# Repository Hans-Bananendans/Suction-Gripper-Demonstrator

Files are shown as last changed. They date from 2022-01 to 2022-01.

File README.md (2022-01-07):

# Suction-Gripper-Demonstrator
Repository that contains a blueprint for a demonstrator model of a bio-inspired, suction-based gripper. This demonstrator was developed by a student team as part of a Bio-Inspired Design MSc course.

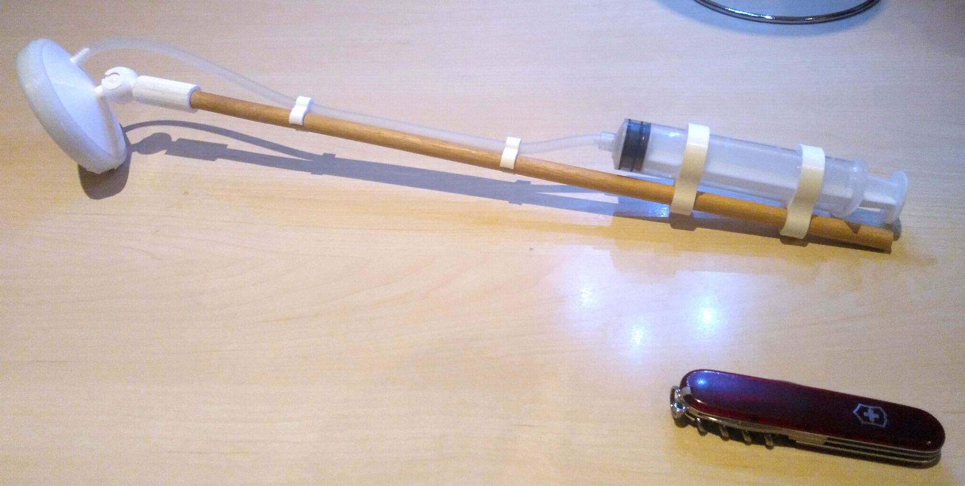
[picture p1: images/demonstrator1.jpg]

_Picture of the demonstrator (Swiss army knife for scale)_

## Description
What this gripper demonstrator is supposed to "demonstrate" is that an array of compliant suction cups can be used to generate substantial gripping force. A miniaturized derivative of such a design could potentially be used in medical applications as a surgical gripper, the current designs of which frequently feature metal "jaws" that often inflict unwanted trauma during surgery due to excess force. A suction-based gripper could spread this force out over a larger area and reduce the chance of complications.

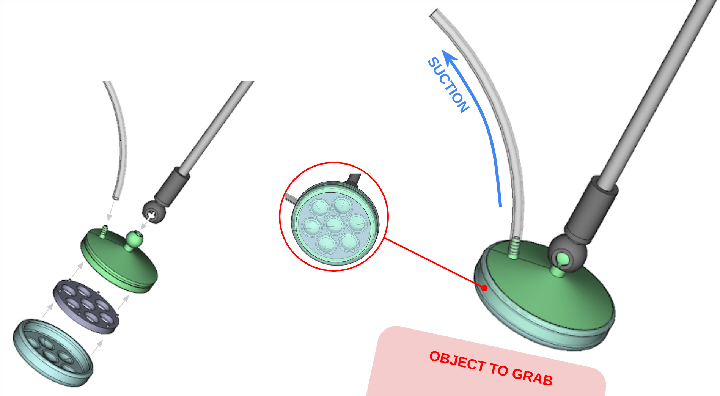
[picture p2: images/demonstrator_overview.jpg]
demonstrator_overview


The demonstrator works as follows: It features a head which can be used to "grip" objects. This head consists of a compliant (~Shore 30) material whose shape can be changed. Inside the head is a sealed chamber, and when pressure in the chamber is reduced, it pulls the compliant material inside. The compliant material is deformed in such a way that it creates suction cups on the other side, which then create a suction force between the head and whatever object is being grabbed. Many cephalopods use a similar principle to attach their limbs to many different objects, and as such, this design was inspired by these animals.

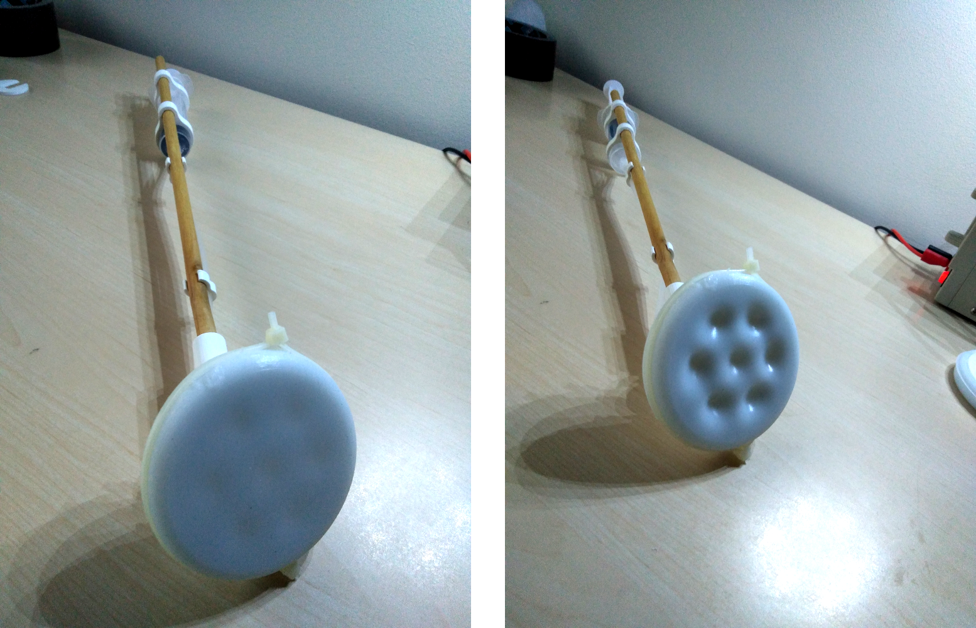
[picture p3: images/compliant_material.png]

_Compliant head of the suction gripper in action. On the right, the syringe is used to reduce the pressure in the suction head to create small suction cups._

## Printable components
For the demonstrator model, some parts will have to be printed. This can be done out of PLA, and the printer does not have to be terribly fancy. The author used an Ender 3 Pro printer for all prints. The STL-files for the prints can be found in the `./STL/` folder.

To build the depicted demonstrator model, you will need to print the following parts:
| Qty | Part | Comment |
| --- |:---|:---|
| 1 | `silicone_mould_bottom_v2.stl` | Print such that the side with the casting negative is pointing up. |
| 1 | `silicone_mould_top_v2.stl` | Print such that the side with the casting negative is pointing up. |
| 1 | `silicone_mould_funnel.stl` | Print with the small side pointing up. |
| 1 | `stick_socket.stl` | Print such that the joint socket is pointing up. |
| 1 | `suction_head_casing.stl` | Print with the ball joint pointing up. |
| 1 | `suction_head_gridcover.stl` | Print with the small knobs pointing up. |
| 2 | `syringe_coupler.stl` | - |
| 2 | `tube_coupler.stl` | - |
| 1 | `syringe_lock.stl` | Optional if you want to lock the syringe in place. |

Printing settings used by author:
 - 20% filler or more.
 - <20 mm/s speed
 - <0.2 mm layer height
 - 1.2 mm wall thickness
 - Use tree supports for everything.

## Component list
**Materials/consumables**
 - 1 30 mL medical syringe
 - ~0.5 meters of medical tubing (4.5 mm inner diameter)
 - A mounting stick. The author used a 400 mm long wooden stick of 9.5 mm diameter.
 - PLA parts as listed above.
 - Super glue (such as cyanoacrylate).
 - Silicone-based kit or glue (the author used [Bison Poly Max](https://www.bison.net/en/product.6310168)). Many other glues (epoxy, cyanoacrylate, etc.) will **NOT** bond with silicone!
 - Latex/vinyl gloves.
 - Some zip ties.
 - Pourable silicone mix (the author used [Wilsor two-component silicone](https://www.wilsor.nl/product/siliconen-rubber/)).
 - Mixing cup for the silicone casting.
 - A stirring implement such as a wooden stick, for the silicone casting.
 - Kitchen scales.
 - Paper towels.

**Tools**
 - Duct tape.
 - Gluing clamps.
 - 120 grit and 400 grit sandpaper.
 - Vaseline.
 - Small files.
 - Hobby knife/army knife.
 - Calipers.

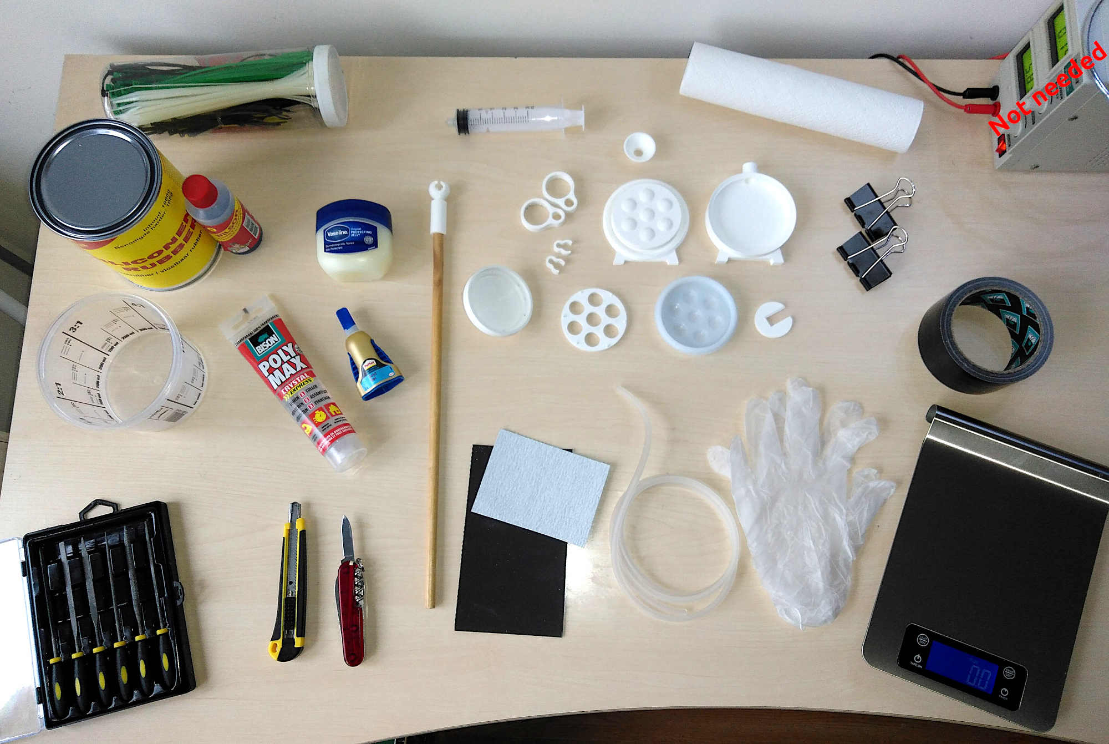
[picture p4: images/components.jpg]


## Manufacturing and assembly

1. First print the parts, as this will take the most time. Gather all the other required tools in the meantime.

### Post-processing the 3D printed parts
2. Remove the excess supports on the printed parts.
3. Test the fit of the `suction_head_casing` and the `suction_head_gridcover`. Remove excess material from the outer edge and the six knobs of the `suction_head_gridcover`, and ensure that the six holes in the `suction_head_casing` are large enough. In the end, you should have a snug fit.
4. Carefully remove the excess material from the outer tube gasket, so that it will not leak when a tube is attached to it.
5. Sand the ball joint until smooth.
6. Using the 120 grit sandpaper, smooth the inner surfaces of the mould halves. Then continue this using 400 grit wet sanding, until the inner surfaces are nice and smooth. Any irregularities in these surfaces will show up in the silicone component as well so to prevent leaks, ensure that the inside of the mould is nice and smooth.
7. Using a small amount of super glue, bond the mould funnel to the mould bottom part. This will form the channel into which the silicone mixture will be poured. The mould is designed such that this channel is also the only riser, allowing for bubbles to escape from the same hole. The funnel will also ensure an excess of silicone at the top, allowing the fluid pressure to force the silicone into the mould.

### Casting the silicone component
8. Coat the inside of the mould with a thin layer of vaseline, so that the silicone cast will release easily. 
9. Close the mould halves and fix them in places using duct tape and/or gluing clamps. The mould is designed with inclined edges such that the two parts will centre by themselves. Ensure that the little feet on both sides of the mould align with one another properly, otherwise the mould will wobble during the casting process. 
10. Put on your gloves. Weigh off around 40-50 grams of silicone base, and mix it with the hardening component in the mixing ratio specified by the manufacturer. For the Winsor silicone used by the author, the base:hardener mixing ratio is 40:3. Stir for a few minutes until the components are thoroughly mixed.
11. Carefully pour the silicone mixture into the mould. You have about 15 minutes to do this before the silicone grows too inviscid to fill the mould properly. If you are unsuccessful, you can just wait for the silicone to harden, remove it, and repeat steps 8 through 11. Once the mould is full, repeatedly tap the mould on a hard surface to help any bubbles flow up and out of the mould. Afterwards, place the whole thing on its feet on a level surface, and let it cure for a few hours.
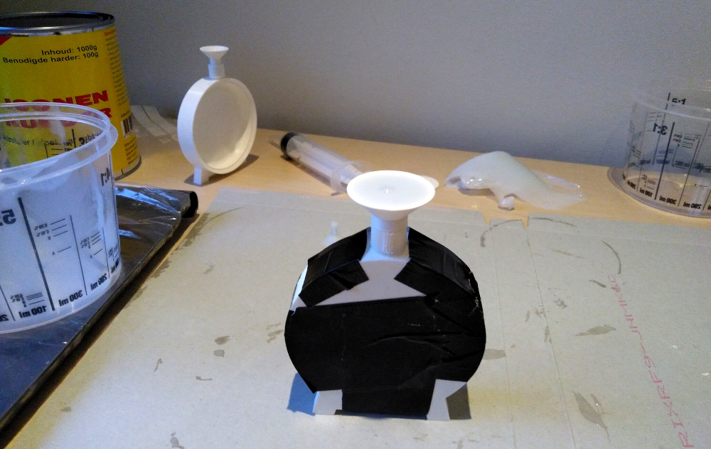
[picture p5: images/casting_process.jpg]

_Filled mould just after casting. Note the air bubble escaping at the top._

12. After the silicone has cured, break the glue connection between the funnel and the mould, either by twisting or cutting with a knife. Also cut through the layer of excess silicone.
13. Remove the clamps/duct tape, and gently separate the mould halves. The silicone part should come loose relatively easily, although you may have to tug a bit harder near the edges.
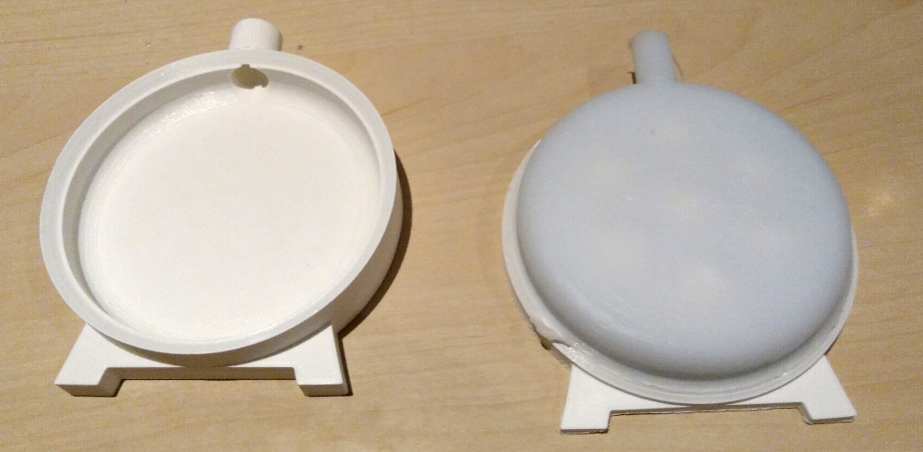
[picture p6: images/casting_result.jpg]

_Cured silicone cast just after removing one of the mould halves. Note the "umbilical cord" of excess silicone at the top._

14. Cut off the excess "umbilical cord" of silicone on the side of the cast. Be **very careful** however that you do not cut through the cast itself, as this will compromise the vacuum seal later on. Better safe than sorry.

### Assembling the suction head

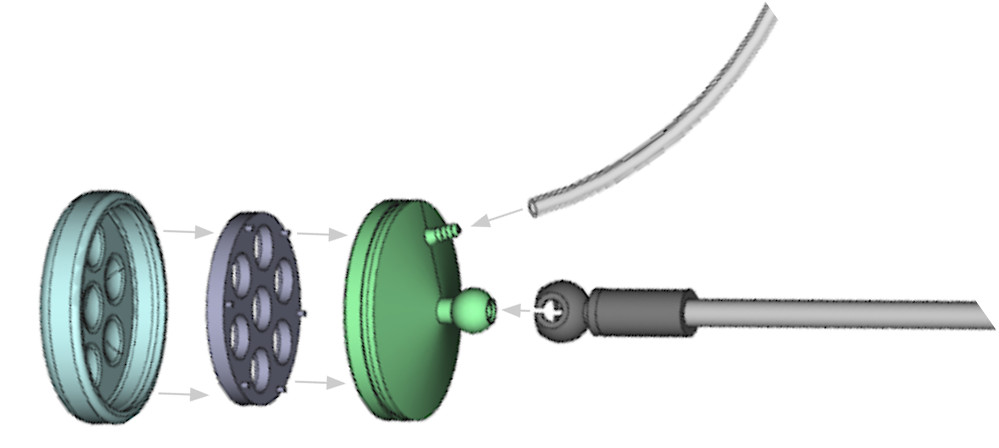
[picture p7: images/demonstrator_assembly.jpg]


15. Insert the `suction_head_gridcover` into the `suction_head_casing`. In the end, the gridcover should be flush with the casing.
16. Apply a liberal amount of silicone kit to the outer edge of the casing, where the silicone part will touch the casing. Spread out the kit until it is distributed evenly. Slide the silicone part over the casing. Fix it in place with zip ties. Leave to cure for at least two hours.
17. Test the quality of the seal by connecting a small length of tubing to the fitting on the casing, and the other end to a syringe. Pull the plunger and see how quickly air rushes in again. If this is in the order of seconds, consider re-gluing the part. This is without a doubt the most frustrating part of the build, and the author ended up building two head parts before managing a good enough seal with the glue.

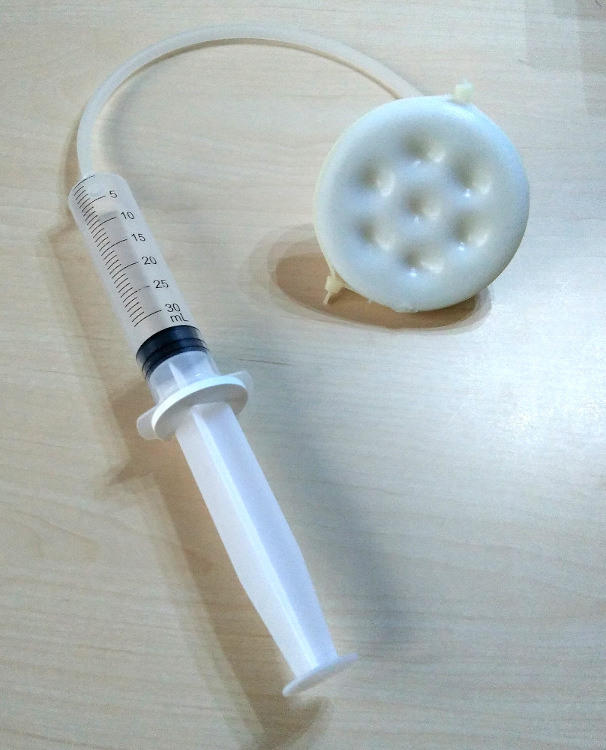
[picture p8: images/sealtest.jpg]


### Assembling the prototype
17. Fit the `stick_socket` part onto the mounting stick. For me a friction fit was enough, but feel free to use glue if necessary.
18. Sand-fit the two `syringe_couplers` until they fit onto the syringe. Then insert the small holes of the `syringe_couplers` onto the mounting stick.
19. Cut a length of surgical tubing to size and fit one end to the syringe, and the other end to the fitting on the suction head.
20. Click the ball joint into place (take care you do not injure your fingers!).
21. Neatly manage the tube by using some of the `tube_couplers`.

That's it. By now you should have the suction gripper demonstrator.

## Demonstration
In the figures below you can see the gripper demonstrator being used to lift the can of silicone base from which it was made. The can was around 877 grams at the time of the test, which the gripper handled easily.
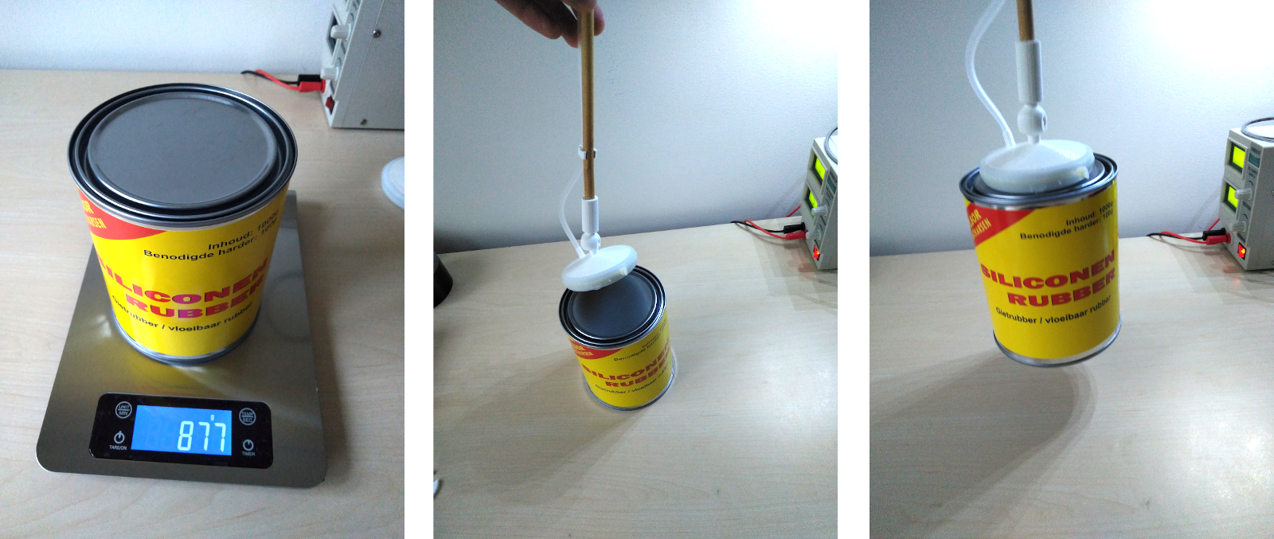
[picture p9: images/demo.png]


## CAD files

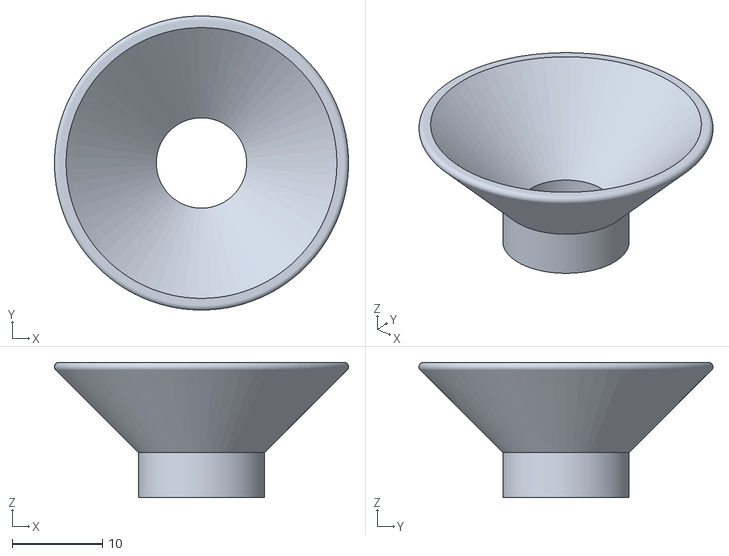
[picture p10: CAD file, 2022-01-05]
STL/silicone_mould_funnel.stl
32.6 x 32.6 x 15.0

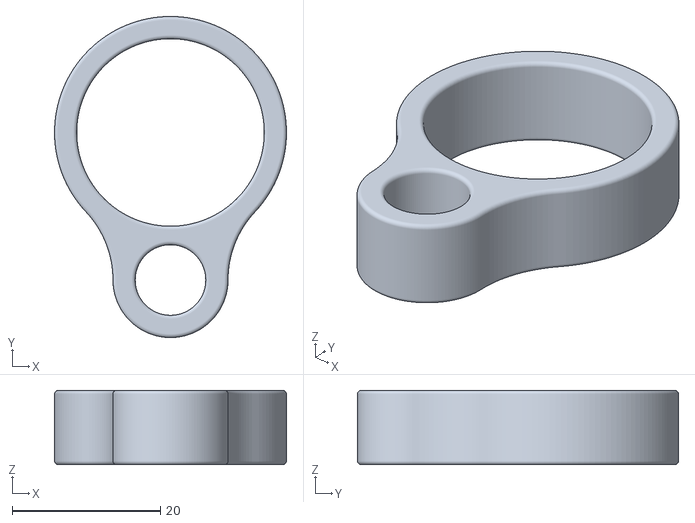
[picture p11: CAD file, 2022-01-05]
STL/syringe_coupler.stl
31.2 x 43.2 x 10.0

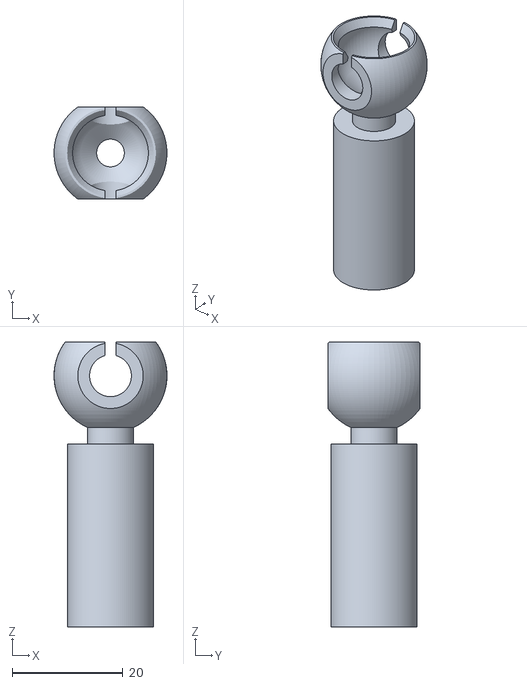
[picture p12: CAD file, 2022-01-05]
STL/stick_socket.stl
20.4 x 16.6 x 51.4

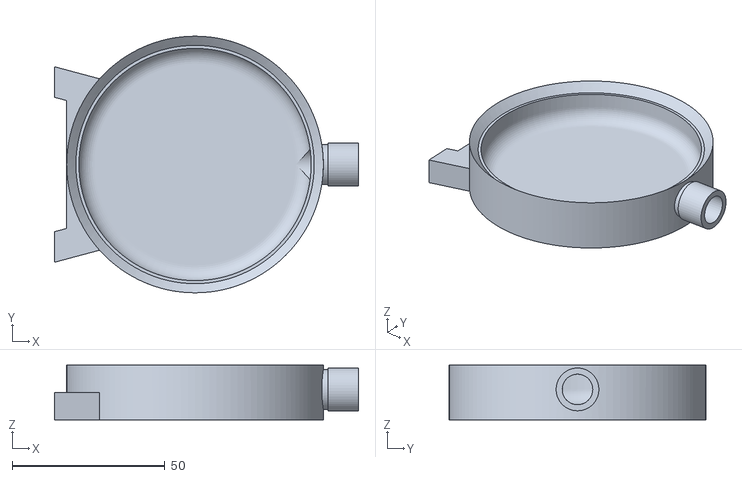
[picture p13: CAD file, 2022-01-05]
STL/silicone_mould_bottom_v2.stl
99.5 x 84.0 x 18.0

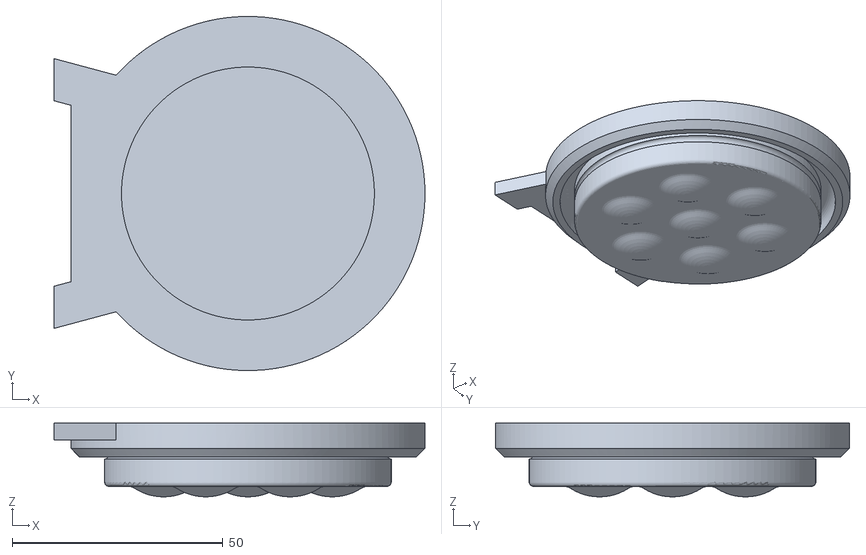
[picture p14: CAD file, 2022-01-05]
STL/silicone_mould_top_v2.stl
88.0 x 84.0 x 17.5

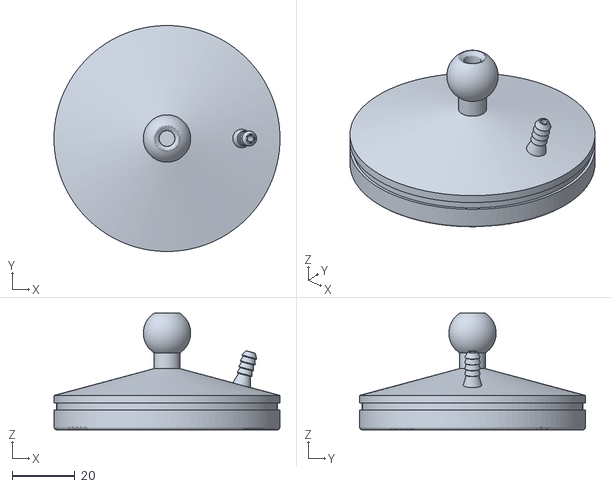
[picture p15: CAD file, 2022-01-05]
STL/suction_head_casing.stl
72.0 x 72.0 x 37.2

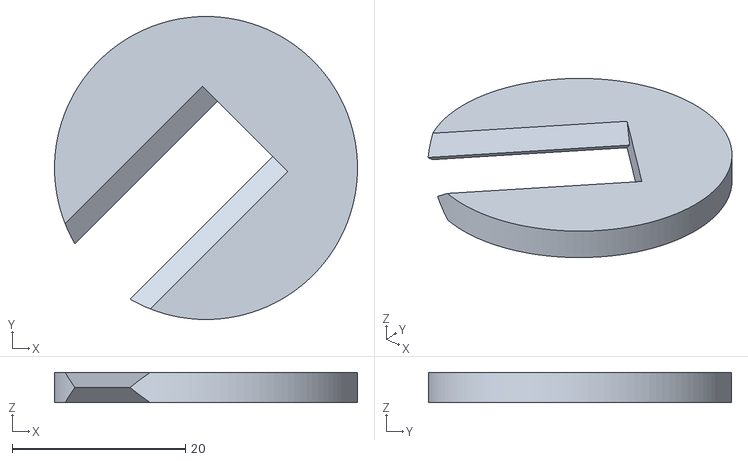
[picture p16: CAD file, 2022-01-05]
STL/syringe_lock.stl
35.0 x 35.0 x 3.50

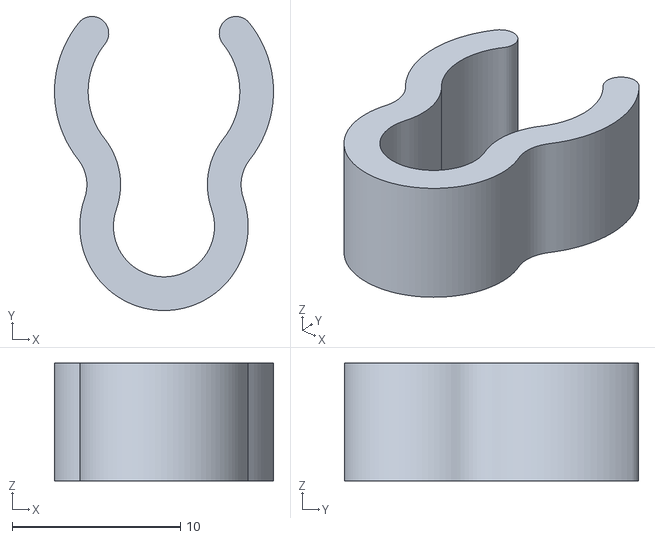
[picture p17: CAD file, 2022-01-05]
STL/tube_coupler.stl
13.0 x 17.5 x 7.00

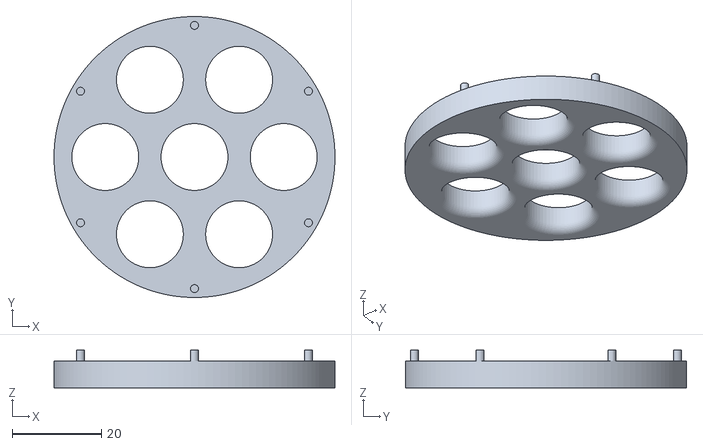
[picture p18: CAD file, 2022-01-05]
STL/suction_head_gridcover.stl
63.0 x 63.0 x 8.50
